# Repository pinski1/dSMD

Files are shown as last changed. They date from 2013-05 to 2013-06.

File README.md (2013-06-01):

#dSMD#
#####dSpin Stepper Motor Driver#####

This is a triple axis stepper motor driver board based on the L6470 chip.

The L6470 is a very advanced stepper motor driver chip. It can be controlled accurately though an SPI interface. Through this interface acceleration, deceleration, maximum speed and minimum speed can be programmed in. This then allows the user to simply command the chip to move the motor in a specific direction by 'n' number of steps. Alternatively a target speed or a target position may be set. The aim is to reduce the overhead on the host processor for motion control.

This board puts 3 of these fantastic chips together on a single PCB. This should be ideal for a CNC or 3D printer with steppers requiring up to 3 Amps each.

Please note:
* That should you require a fourth or fifth stepper, say for an extruder/s then this will require a separate board.
* This board has yet to be prototyped so I cannot offer any guarantees of it working.

More information on the L6470 can be found [here](http://www.st.com/internet/analog/product/248592.jsp).

##The Board##
In addition to the 3 stepper motor drivers the board also contains connections for attaching a power supply, 6 limit switches which are also connected to a 10 way IDC header, a 16 way IDC header for connecting to your host processor of choice.

###Dimensions###
The board size is 100mm by 62mm and is compatible with the [Sick of Beige](http://dangerousprototypes.com/docs/Sick_of_Beige_standard_PCB_sizes_v1.0) board size specification.

Due to the heat that can be generated by the 3 L6470 ICs it is not recommended to mount a plastic cover without adequate cooling. It is however recommended to use the board either mounted or with standoffs.

<a name="power-supply-input"/>
###Power Supply Input###
* Motor supply: +8 to +45V at a maximum of 9A
  * The voltage compensation is set for a motor supply of +13V.
* Logic supply: +5V at a maximum of 0.2A

Power can be supplied either via screw terminals or a PC PSU molex connector.

###Endstops Pinout####

|Pin Func|Pin|Pin|Pin Func|
|---:|:--:|:--:|:---|
|GND|1|2|+5V|
|min_x|3|4|max_x|
|min_y|5|6|max_y|
|min_z|7|8|max_z|
|GND|9|10|+5V|

The "min_*" and "max_*" signals are active high signals with 10k pull-down resistors. Note these signals can be monitored by reading the "SW_F" bit in the "STATUS" register of each L6470. The L6470 is set by default to cause a "HARD_STOP" interrupt which stops all movement if the pin SW goes low.

###Control Pinout####

|Pin Func|Pin|Pin|Pin Func|
|---:|:--:|:--:|:---|
|GND|1|2|+5V|
|/flag_x|3|4|SCK|
|/flag_y|5|6|MISO|
|/flag_z|7|8|MOSI|
|step_x|9|10|/cs_x|
|step_y|11|12|/cs_y|
|step_z|13|14|/cs_z|
|GND|15|16|+5V|

* The "/flag_*" signals are active low outputs with a 10k pull-up. This signal will only activate if the bit for the condition is set in the "ALARM_EN" register of the L6470. If this signal does go low then it is recommended to read the "STATUS" register for more information.
* The "step_*" signals are active high inputs. The maximum step frequency that the L6470 will recognise is 2MHz. When the L6470 is sent hte "StepClock" command with a direction of rotation then with every rising edge on step the L6470 will move one microstep in that direction.
* The current revision of the board has 3 seperate "/cs_*" active low inputs for selecting individual L6470s. Future revisions will daisy chain the L6470s to reduce GPIO count.

##Firmware##
This is difficult as it can vary between architectures (AVR, PIC & ARM) as well as between IDEs (MPLab, Arduino, AVR Studio etc). I shall try to add links & relevant bits of code as this project progresses.

Notes:
* The "/cs_*" line must be raised after every byte.
* If you are expecting a response you should send a dummy byte (0x00 or 0xFF).
* The L6470 requires both power supply rails, +12V and +5V to operate.

###Debugging###
1. Disconnect everything.
2. Connect the motor and logic supplies. LED1 should light if there is a voltage on the logic supply. LED2 should light if there is a voltage on the motor supply.
3. Use a multi-meter to confirm the voltages are within acceptable ranges. See the power supply section [above](#power-supply-input).
4. Connect the host processor and attempt to get it to read the status register.

##Licence##
<br /><span xmlns:dct="http://purl.org/dc/terms/" property="dct:title">dSMD</span> is licensed under a <a rel="license" href="http://creativecommons.org/licenses/by-sa/3.0/deed.en_US">Creative Commons Attribution-ShareAlike 3.0 Unported License</a.>

This project is an [Open Source Hardware Project](http://www.oshwa.org/definition/).

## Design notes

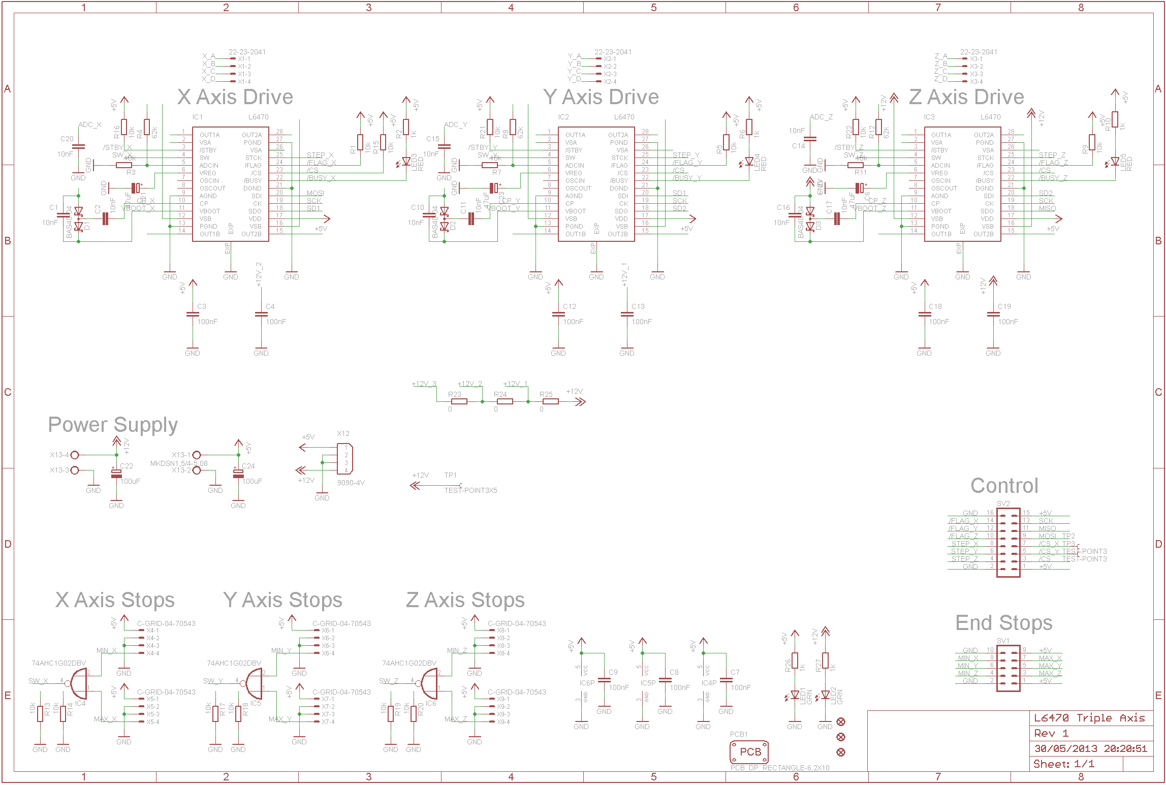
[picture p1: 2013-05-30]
Hardware/dSMD Schematic.png

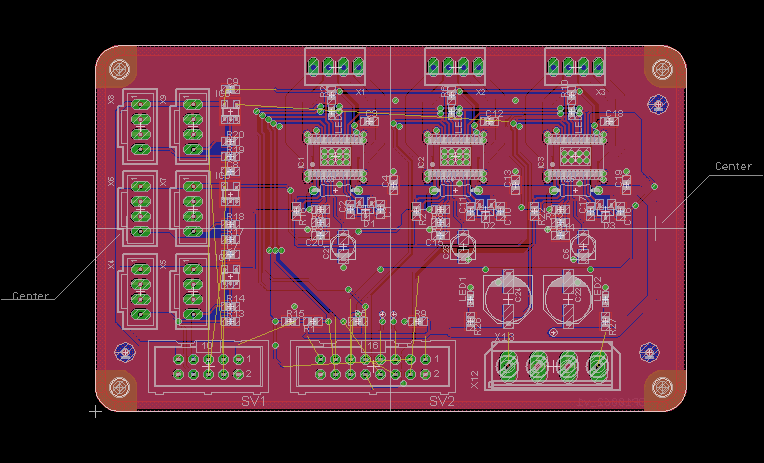
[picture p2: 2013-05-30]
Hardware/dSMD PCB.png

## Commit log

2012-05-20 Initial test Commit.
    [Rev 1.brd, Rev 1.sch]
2012-06-18 Quick tidy up
    [Rev 1.brd, Rev 1.sch]
2012-06-18 Should have read the datasheet
    [Rev 1.brd, Rev 1.sch, Rev 1.xls]
2013-05-30 Reorganising, PCB shrinking and image generating
    [Rev 1.brd, Rev 1.sch, Rev 1.xls]
2013-06-01 Added some basic debugging advice.
    [Rev 1.brd, Rev 1.sch]
